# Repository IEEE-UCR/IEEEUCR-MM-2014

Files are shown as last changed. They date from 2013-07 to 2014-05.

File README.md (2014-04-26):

IEEEUCR-MM-2014
===============

In order to create better, exciting micromice, it is necessary to pool together work in order to create better programs to run on micromice.

This repository has folders for all current micromice.  Some may have been abandoned in favor of better mice (refmouse V1).

Although it is difficult to admit to the utter data-copying, a lot of the kicad libraries are copied.

Within the hardware realm, KiCAD is the de facto standard for making PCBs.  When micromice get really big, it's absolutely essential to choose a program that allows multipage schematics.

And through these methods, we will create better micromice.

Documentation is also provided through the documentation folder... in case anybody wants to read it.

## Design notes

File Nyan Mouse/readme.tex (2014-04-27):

\documentclass{article}
\usepackage[UKenglish]{babel}
\usepackage{parskip}
\usepackage{indentfirst}
\setlength{\parindent}{15pt}
\usepackage{fullpage}
\setcounter{tocdepth}{3}
\begin{document}
\title{Nyan Mouse Readme}
\author {Brandon Lu} \date{\today}
\maketitle
\begin{abstract}
Nyan Mouse is made to display Nyan Cat like blinking and audio.  From a hardware perspective, Nyan Mouse will offer an FPGA with a Nios II processor implemented on it along with some peripherals for quaterature decoding (including count and inter-step delay for speed).  Everything should be capable of parallel-execution including maze solving.  Maze solving, due to time constraints, will not be implemented in a hardware accelerated form.  This will be Brandon's micromouse entry for 2014 if it is completed.  Otherwise, Overvolt will be the micromouse of choice for racing.
\end{abstract}

\section {Introduction}
Micromouse as a competition creates an environment that requries the harmonious marriage between hardware and software.  There are many arguments that feature software or hardware as the superior micromouse success determiner, but in the end a micromouse simulator that is beautifully coded exists only in the computer and a hardware implementation with the best hardware imaginable including support for wall decoding and time delayed illumination is only a brainless device that goes forward nonstop at an unimaginable speed (probably to crash into the wall ahead of it).  Micromouse is not a simple thing to do in any sense unless one decides to make it simple (and ignore the fine detail present in any of the advanced topics which it can cover).  The most important thing to have during micromouse is probably time management; humans -- especially college humans -- are only given a finite amount of time on micromouse.  It is possible to extract time from other things, but that can end in disaster quite easily.

\section {Implementing the Cat}
\subsection {Hardware}
The hardware on this micromouse is fairly complex and a full explanation of the hardware cannot be achieved easily.

In short, the main board contains the non-controller parts of nyan mouse.  This includes parts such as the motors, drive train, encoders, speakers, LEDs, and other rather important parts that have absolutely nothing to do with making a functional micromouse but instead add quirky features to a micromouse.

\subsection {Software}
The software on this mouse will be my old software that ran on Overvolt.
The software is actually quite craptastinc in that it does not support full encoder guidance or mapping.
In fact, only one encoder was used because of circuit design errors encountered while not considering the therevin equivalence models of the quaterature encoders inside the Faulhaber motors.

\section {Nyaning and Catting (Methods)}
Nyanning and catting is achieved with the use of CAD software and implementation of the \textit{Cyclone IV Handbook} along with various application notes such as those from Spansion (which creates the flash ROM).

Autodesk Inventor 2013 is used to do the 3D design of the micromouse (and will hopefully do the printed circuit board stacks as well).

Altera Quartus is used to instantiate the FPGA internals including the Nios II cores.

Altera Nios II developer (based on eclipse) is used to program the Nios II processor and generate the programming files.

KiCAD is used to generate the actual printed circuit boards (this makes a significant portion of available PDF documentation because of the ease in exporting KiCAD to schematic).

\section {Is there any win to this game?}
Nyan Cat as a game itself (if one can consider it a game), has no end but a definite beginning.  By default, the counter on the nyan cat webpage will keep incrementing (perhaps until it overflows at some very large number).  The purpose of this document was to explain what one would find in the micromouse folder and how it's supposed to work, but I forgot to do that and instead went on about the philosophy of micromouse.

\end {document}

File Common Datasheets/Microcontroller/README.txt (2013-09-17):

Our microcontroller will most likely be the STM32F4
http://www.st.com/web/en/catalog/mmc/FM141/SC1169/SS1577

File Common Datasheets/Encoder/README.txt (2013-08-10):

IEEE UCR has decided to, on its first mouse at least, use a precision magnet and a 10bit magnetic rotary decoder.

Magnetic Rotary Position Sensor: http://www.ams.com/eng/Products/Magnetic-Position-Sensors/Rotary-Magnetic-Position-Sensors/AS5040

Precision Magnet: http://www.ams.com/eng/Products/Magnetic-Position-Sensors/Magnets3/AS5000-MD6H-3

Somebody who has already done this before: http://xmog123x.blogspot.com/2012/11/kirin-micromouse.html

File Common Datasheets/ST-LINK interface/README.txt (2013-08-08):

How we do STLink
================

The STLink adapter interfaces to a boxed 2x10 header with 2.54mm (1 mil) pitch.  This interface is too large for our purposes.

So instead we have a 1.0mm device interfacing to these signals.

When the time comes, we will have a device interface on the IEEUCR website for all to use.

"At this point 8/8/2013 I have no idea how to use STLink" -- Brandon.

It should be noted that although we do have a SWIM interface that we could use instead of the 20 pin awesomeness, we need debugging.

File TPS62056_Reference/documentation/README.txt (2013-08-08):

Voltage Regulator
=================

The voltage regulation circuit is designed to be portable across different KiCAD builds of micromouse.

This folder contains our reference board and some PDF's.  We may have some waveforms available for it too.

Our test results show a clearly bruteforceable and well designed regulator.

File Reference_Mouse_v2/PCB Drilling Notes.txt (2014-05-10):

Bluetooth header has traces going to the top

Drill bit sizes
Pin headers: 1.00mm
LED/PTH leads: 0.70mm
Via holes: 0.6mm

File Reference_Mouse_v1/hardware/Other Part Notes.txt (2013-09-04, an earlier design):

[LED Alphanumeric Display]
Avago HCMS-39xx series (HCMS-29xx series is the 5v-powered version)
5x7 dot matrix
Basically a giant shift register for each pixel + some control registers 
Easily drivable using SPI + DMA
Example: http://www.micromouseonline.com/2012/03/11/adding-dma-to-the-spi-driver-with-the-stm32f4/#axzz2cIIhLh9E

[Motor Drivers]
DRV8837
Control inputs (each)
	IN1 & IN2 (internal pulldowns)

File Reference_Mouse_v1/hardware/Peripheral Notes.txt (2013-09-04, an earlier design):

[Timer assignments]
TIM1 (Advanced control)
	Motor PWM x 2

TIMx (general purpose)
	Quadrature decoder x 1

TIMx (general purpose)
	Quadrature decoder x 1

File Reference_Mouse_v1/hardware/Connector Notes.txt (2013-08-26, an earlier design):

It seems like every small DC connector attached to a battery gets called a "JST", which is not very helpful.
http://www.rcgroups.com/forums/showthread.php?t=1493712

Lipo balance plugs are always "JST-XH"
	Easily recognized: 2.5mm pitch and "hooks" on the plug and recepticicle
	PCB-mount top-entry receptacle is B3B-XH-A (not B3B-XH-AM, that one has board-insertion orientation pin)
	Bal-plug pinout: http://goo.gl/ZAvH9i
		I'm going to call the top pin #1 so it stays GND

The protected 1S lipos and accessories sold by Sparkfun are NOT JST-XH (they are some other 2mm pitch JST)
	(Their 2S RC-style packs, however, do have JST-XH balance connectors)

The 2-pin red "JST" with beveled edges on the top?
	Those are actually "RCY connectors", manufactured by JST
	These are wire-to-wire only. There does not seem to be a PCB-mount version of these

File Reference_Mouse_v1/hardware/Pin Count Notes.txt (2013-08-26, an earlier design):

[Estimated Pin Count Requirement]

* 6 IR sensor pairs
1-6 (6):  IR Emitters enable
7-12 (6): IR Detectors ADC

* 2 motors with quadrature encoders"
* 3 pins per motor allows flexible drive topologies (sign-mag, locked antiphase, etc)
13-16 (2x2): Wheel Encoders, quadrature
17-22 (2x3): Motor drivers

* SPI devices
23-25 (3): SPI bus (MOSI, MISO, SCK)
26-27 (2): Avago serial display (Chip select, Register select)

* I2C devices
28-29 (2): I2C bus (SCK, SDA)
	MPU-6050 Gyro + Accel (400 KHz, 2.38V-3.46V)
	HMC5883L Mag (400 KHz, 2.16V-3.6V)
	Run I2C bus and devices off 2.8V linreg? STM32 capable of 2.8V levels.

30-31 (2): UART (TX, RX)
	Bluetooth + serial bootload ("JY-MCU")

32 (1): MPU-6050 Interrupt

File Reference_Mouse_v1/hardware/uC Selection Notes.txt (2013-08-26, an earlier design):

[STM32 F1 Line - Cortex M3]
STM32F100 Value line  – 24 MHz CPU with motor control and CEC functions
STM32F101 – 36 MHz CPU, up to 1 Mbyte of Flash
STM32F102 – 48 MHz CPU with USB FS
STM32F103 – 72 MHz, up to 1 Mbyte of Flash with motor control, USB and CAN
STM32F105/107 – 72 MHz CPU with Ethernet MAC, CAN and USB 2.0 OTG

STM32VLDISCOVERY chip is STM32F100RB
Maple chip is STM32F103RB (LQFP64)
	"Medium density"
	* 72 MHz Cortex-M3
	* 128 KB flash
	* 20 KB SRAM
	* 3 GP timers
	* 1 Adv. control timers
	* 2 x SPI
	* 2 x I2C
	* 3 x USART
	* USB
	* CAN bus
	* 51 GPIOs
	* 2 x 12-bit adc, 16 channels
	* 2.0V to 3.6V

[STM32 F4 Line - Cortex M4F]
STM32F4DISCOVERY chip is STM32F407VGT6 (LQFP100)

Alternatively, use STM32F405RG (LQFP64)
	Same core and peripherals
	Smaller package, to match F1 drop-in replacement
	Still more than enough ADC channels and GPIOs
	No external memory controller, but not needed
	* 168 MHz Cortex-M4F
	* 1 MB flash
	* 192 KB SRAM
	* 10 GP timers
	* 2 Adv. control timers
	* 2 Basic timers
	* Random number gen
	* 3/2 (f/d) x SPI
	* 3 x I2C
	* 4/2 x USART
	* USB
	* 51 GPIOs
	* 3 x 12-bit adc, 16 channels
	* 1.8V to 3.6V

http://www.micromouseonline.com/2009/12/29/arm-stm32-jtag/#axzz2cJiC3gTI

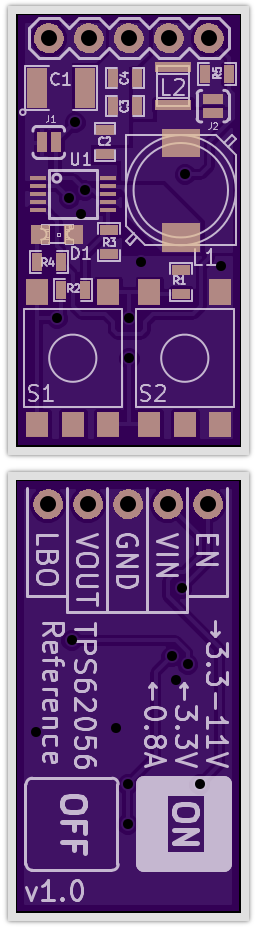
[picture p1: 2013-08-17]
TPS62056_Reference/hardware/Oshpark Preview.PNG

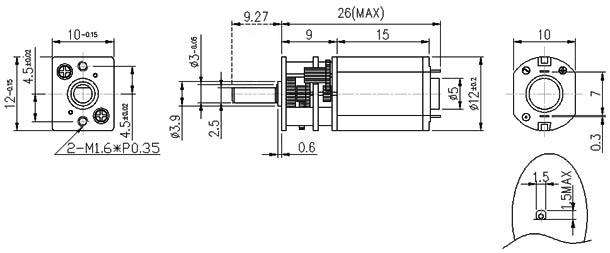
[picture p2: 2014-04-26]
Common Datasheets/Motor/Pololu Micro Metal Gearmotor Dimensions (similar to Sanyo).png

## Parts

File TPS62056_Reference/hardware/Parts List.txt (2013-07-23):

----[ Notes ]----

Ripple at 8.4v to 3.3v w/ 10uH inductor
0.24A

Module pinout:
1. Enable                 _
2. Vin (3-pin regulator)   |
3. Gnd (3-pin regulator)   | Silkscreen box
4. Vout (3-pin regulator) _|
5. Low-Battery Out

----[ User Manual ]----

Things to add to your circuit:

Reverse polarity protection:
In the form of a low-voltage drop diode or MOSFET-based circuit
Why is it not in the module?
Both of the above mentioned components introduce some form of inefficiency and cost more.
Diodes have a voltage drop, MOSFETs have on-resistance and 
In addition, you will most likely connect your motor drivers directly to the battery
while the switching regulator powers the logic and sensors. Integrating reverse polarity protection into the module will not protect those components.
If you want, you can add a diode to your circuit while you prototype or final circuit
But you should use polarity-coded connectors for your batteries anyway.
And just be careful.

Saving power:
The power LED lets you see at a glace whether the circuit is powered. But if your project needs to run for the longest time posible on a battery charge, this will save a few mA.

Not populating the LBI voltage divider nor the LBO pull-up will net you few microamps, but this should rarely be necessary.

Staying on:
If you already have an external power switch, shorting J1 and not popluating either pushbutton will cause the module to turn on whenever power is applied, thus acting like a regular 3-pin regulator.

Software-controlled shutdown:
Using an additional transistor, you can have your microcontroller turn off it's own power by momentarily pulling the Enable pin to ground through a 10K resistor. The resistor prevents a battery-to-ground short if the module's "On" button is pressed at the same time). The pushbutton causes full battery voltage to appear on the Enable pin, do not connect the enable pin directly to your microcontroller.
[insert diagram here]

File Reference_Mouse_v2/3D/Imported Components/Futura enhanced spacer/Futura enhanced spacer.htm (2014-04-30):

Autodesk Inventor Translation Report | Monday, April 28, 2014 (6:05 PM)
Source File: | C:\Users\Kevin\Downloads\futura-3D-printing-model\Futura enhanced spacer.stl
Translator Type: | STL | Sending System:
Author: |  | Translation Time: | 00:00:02
Options
Import Type: | N/A
Entity Types to Import: | Meshes
Import into Repair Environment: | N/A
Import Assembly as Single Part: | N/A
Create Surfaces As: | N/A
Import Multiple Solid Parts as Assembly: | N/A
Check Parts during Load: | N/A
Auto Stitch: | N/A
Enable Advanced Healing: | N/A
Color Red/Green/Blue Order: | RGB
+/- | Name | Inventor File | Status
[ ] | Futura enhanced spacer.ipt | C:\Users\Kevin\Dropbox\IEEEUCR-MM-2014\Reference_Mouse_v2\3D\Imported Components\Futura enhanced spacer\Futura enhanced spacer.ipt | Successful

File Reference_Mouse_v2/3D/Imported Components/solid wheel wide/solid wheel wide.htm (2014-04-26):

Autodesk Inventor Translation Report | Wednesday, April 23, 2014 (12:45 AM)
Source File: | C:\Users\Kevin\Downloads\futura-3D-printing-model\solid wheel wide.stl
Translator Type: | STL | Sending System:
Author: |  | Translation Time: | 00:00:00
Options
Import Type: | N/A
Entity Types to Import: | Meshes
Import into Repair Environment: | N/A
Import Assembly as Single Part: | N/A
Create Surfaces As: | N/A
Import Multiple Solid Parts as Assembly: | N/A
Check Parts during Load: | N/A
Auto Stitch: | N/A
Enable Advanced Healing: | N/A
Color Red/Green/Blue Order: | RGB
+/- | Name | Inventor File | Status
[ ] | solid wheel wide.ipt | C:\Users\Kevin\Dropbox\IEEEUCR-MM-2014\Reference_Mouse_v2\3D\Imported Components\solid wheel wide\solid wheel wide.ipt | Successful

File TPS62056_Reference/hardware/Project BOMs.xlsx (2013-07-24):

Supplier | Supplier Part # | Description | Package | Designators | Cost / Unit | Qty / Board | Item Cost / Board | Total Qty | Notes
Mouser | 810-C3225Y5V1C226Z-9 | MLCC 22uF, 16V, 20% | 1210 | C1 | $0.29 | 1 | $0.29 | 3
Mouser | 810-C1608X5R0J226M | MLCC 22uF, 6.3V, 20% | 0603 | C2, C3, C4 | $0.15 | 3 | $0.45 | 9
Mouser | 720-LSR976-NR-1 | LED Red Clear Diffused Std., 2.0V, 25mA | 0805 | D1 | $0.05 | 1 | $0.05 | 3 | (Quantity 10 price bracket)
Mouser | 652-SRR7032-100M | Inductor 10uH Shielded, 20%, 1.4A, 0.068ohm | (non-std.) | L1 | $0.64 | 1 | $0.64 | 3 | http://www.mouser.com/ds/2/54/SRR7032-54455.pdf
Mouser | 542-PM1008-82NK-RC | Inductor 82nH Unshielded, 10%, 1A, 0.22ohm | (non-std.) | L2 | $0.29 | 1 | $0.29 | 3
Mouser | 517-5111TG | Pin Header 40-pin, right-angle 0.1", gold | SIL-5 | P1 | $1.66 | 0.125 | $0.21 | 0.375 | Broken off of a 40-pin header. Can also use straight headers or no headers at all.
Mouser | 667-ERJ-3GEYJ475V | Resistor 4.7 MΩ, 5% | 0603 | R1 | $0.01 | 1 | $0.01 | 3 | (Quantity 10 price bracket)
Mouser | 667-ERJ-3GEYJ514V | Resistor 510 KΩ, 5% | 0603 | R2, R5 | $0.01 | 2 | $0.02 | 6 | (Quantity 10 price bracket)
Mouser | 667-ERJ-3GEYJ114V | Resistor 110 KΩ, 5% | 0603 | R3 | $0.01 | 1 | $0.01 | 3 | (Quantity 10 price bracket)
Mouser | 667-ERJ-3GEYJ331V | Resistor 330 Ω, 5% | 0603 | R4 | $0.01 | 1 | $0.01 | 3 | (Quantity 10 price bracket)
Mouser | 688-SKHMQKE010 | Tactile Switch SMD, NO, 0.98N, Black | (non-std.) | S1, S2 | $0.24 | 2 | $0.48 | 6
Mouser | 595-TPS62056DGS | TPS62056 3.3V Switching Regulator | miniSO-10 | U1 | $3.05 | 1 | $3.05 | 3
Oshpark | (n/a) | PCB | (n/a) | (n/a) | $3.05 | 0.3333 | $1.02 | 0.9999 | Comes as a set of three
 |  |  |  |  |  |  | $0.00 | 0
 |  |  |  |  |  |  | $0.00 | 0
 |  | (All items are priced at quantity 1 unless |  |  |  |  | $0.00 | 0
 |  | otherwise noted) |  |  |  |  | $0.00 | 0
 |  |  |  |  |  |  | $0.00 | 0
 |  |  |  |  |  |  | $0.00 | 0
 |  |  |  |  |  |  | $0.00 | 0
 |  |  |  |  |  |  | $0.00 | 0
 |  |  |  |  |  |  | $0.00 | 0
 |  |  |  |  |  |  | $0.00 | 0
 |  |  |  |  |  |  | $0.00 | 0
 |  |  |  |  |  |  | $0.00 | 0
 |  |  |  |  |  |  | $0.00 | 0
 |  |  |  |  |  |  | $0.00 | 0
 |  |  |  |  |  |  | $0.00 | 0
 |  |  |  |  |  |  | $0.00 | 0
 |  |  |  |  |  |  | $0.00 | 0
 |  |  |  |  |  |  | $0.00 | 0
 |  |  |  |  |  |  | $0.00 | 0
 |  |  |  |  |  |  | $0.00 | 0
 |  |  |  |  |  |  | $0.00 | 0
 |  |  |  |  |  |  | $0.00 | 0
 |  |  |  |  |  |  | $0.00 | 0
 |  |  |  |  |  |  | $0.00 | 0
 |  |  |  |  |  |  | $0.00 | 0
 |  |  |  |  |  |  | $0.00 | 0
 |  |  |  |  |  |  | $0.00 | 0
 |  |  |  |  |  |  | $0.00 | 0
Cost / Item: The cost of one component of this type. (the cost of a single resistor) |  |  |  | Subtotal per board: |  |  | $6.52
Qty / Board: The count of this component that is present on a single board |  |  |  | (n*) Number of boards: |  |  | 3
Item Cost / Board: The combined cost of every one of this component on a single board |  |  |  | Total: |  |  | $19.55
Total Qty: The number of this component that should be ordered to populate n* boards
(Highlight colors chosen by colorblind person. Your milage may vary.)

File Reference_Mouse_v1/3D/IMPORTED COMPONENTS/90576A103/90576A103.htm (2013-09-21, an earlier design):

Autodesk Inventor Translation Report | Saturday, September 21, 2013 (2:42 AM)
Source File: | E:\ENGINEERING\IEEEUCR-MM-2014\HARDWARE\REFERENCE_MOUSE_V1\3D\SOLIDWORKS MCMASTERCARR PARTS\90576A103.SLDPRT
Translator Type: | SolidWorks | Sending System: | SolidWorks 2007
Author: |  | Translation Time: | 00:00:01
Options
Import Type: | N/A
Entity Types to Import: | Solids, Surfaces, Wires
Import into Repair Environment: | Yes
Import Assembly as Single Part: | No
Create Surfaces As: | Single Composite Feature
Check Parts during Load: | No
Auto Stitch: | No
Enable Advanced Healing: | N/A
+/- | Name | Inventor File | Status
[ ] | 90576A103 | E:\ENGINEERING\IEEEUCR-MM-2014\HARDWARE\REFERENCE_MOUSE_V1\3D\SOLIDWORKS MCMASTERCARR PARTS\IMPORTED COMPONENTS\90576A103\90576A103.IPT | Successful

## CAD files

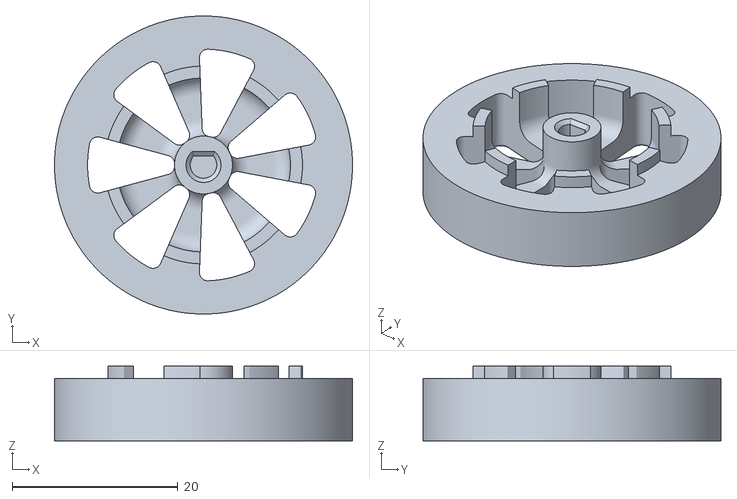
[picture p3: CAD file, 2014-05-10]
Reference_Mouse_v2/3D/Wheel Printable.stl
36.0 x 36.0 x 9.00

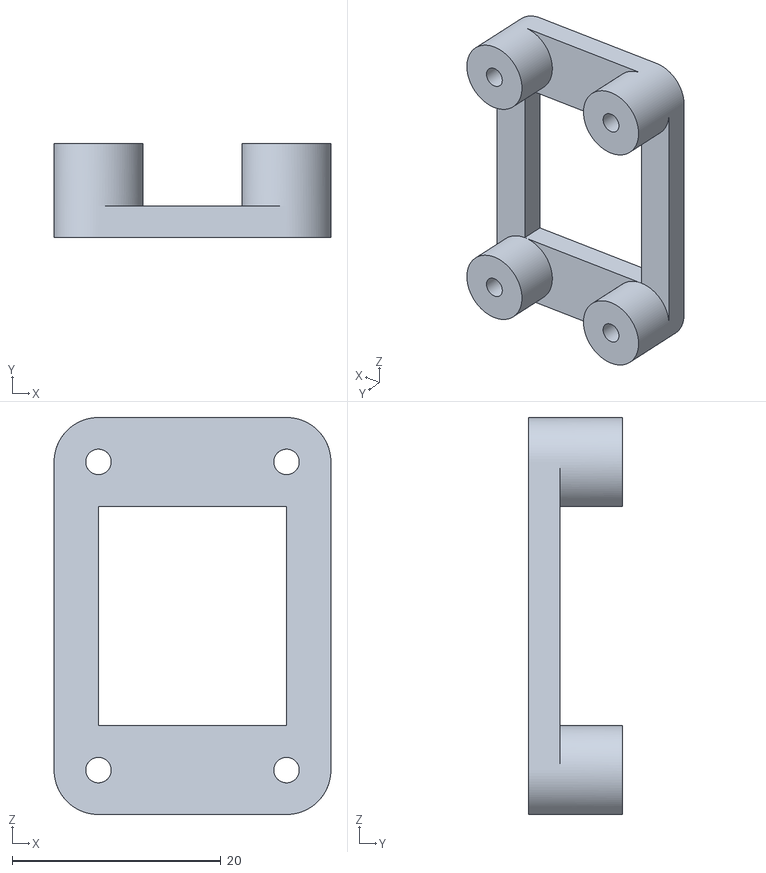
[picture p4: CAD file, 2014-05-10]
Reference_Mouse_v2/3D/Spacer.stl
26.5 x 9.00 x 38.0

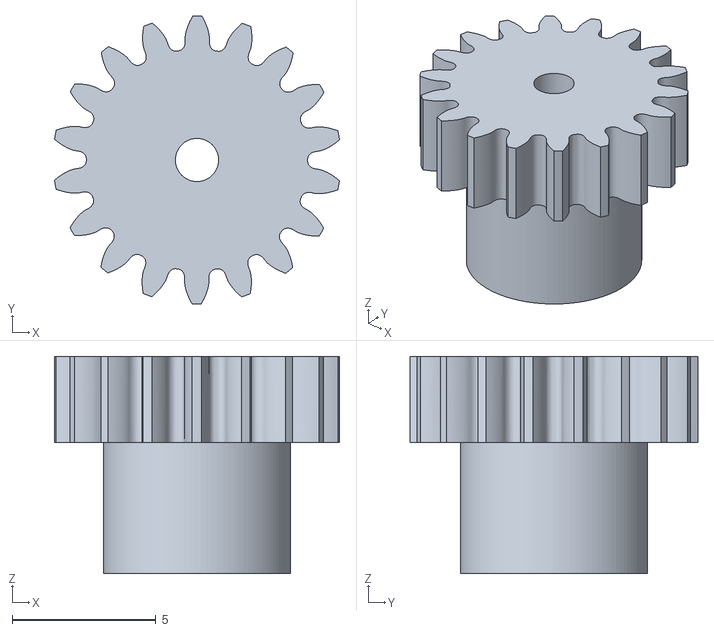
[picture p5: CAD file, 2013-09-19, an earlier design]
Reference_Mouse_v1/3D/mount_gear motor_5.stl
9.90 x 10.00 x 7.55

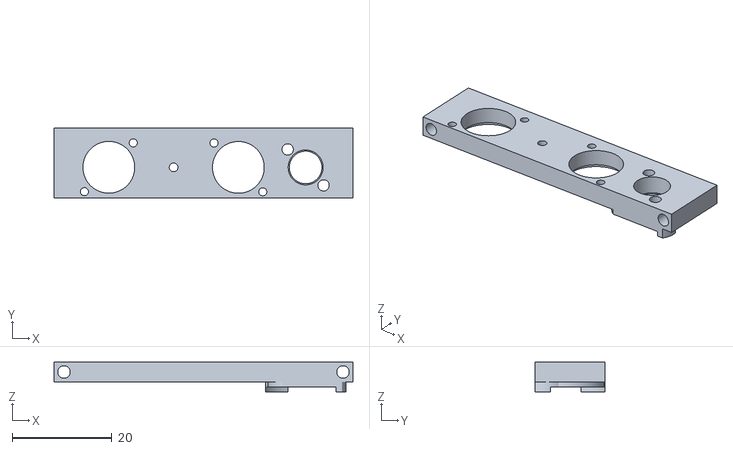
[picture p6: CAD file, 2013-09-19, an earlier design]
Reference_Mouse_v1/3D/mount_mount_4.stl
60.0 x 14.0 x 6.00

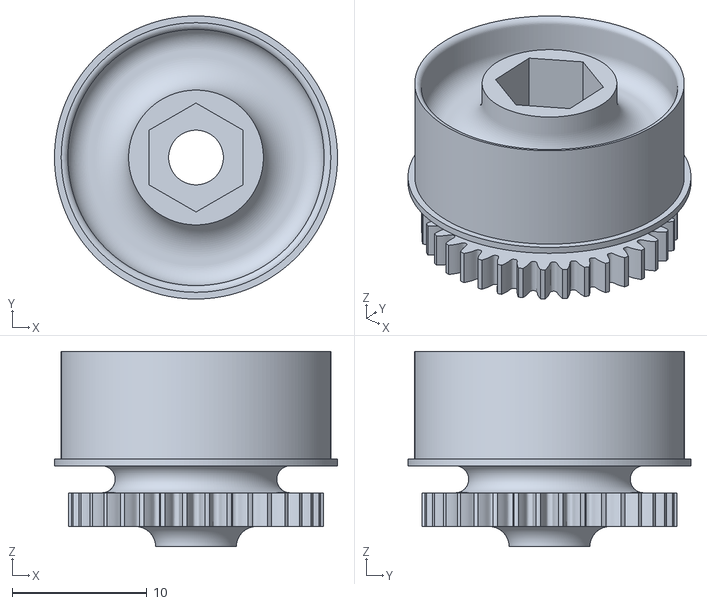
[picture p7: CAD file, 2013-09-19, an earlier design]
Reference_Mouse_v1/3D/mount_Wheel_MIR_3.stl
21.0 x 21.0 x 14.5

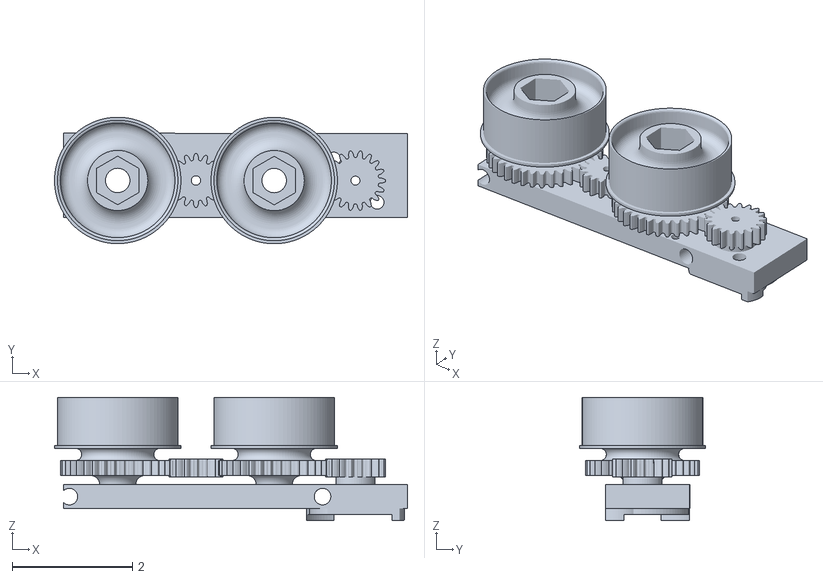
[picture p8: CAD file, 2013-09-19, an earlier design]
Reference_Mouse_v1/3D/mount.stl
5.86 x 2.10 x 2.05

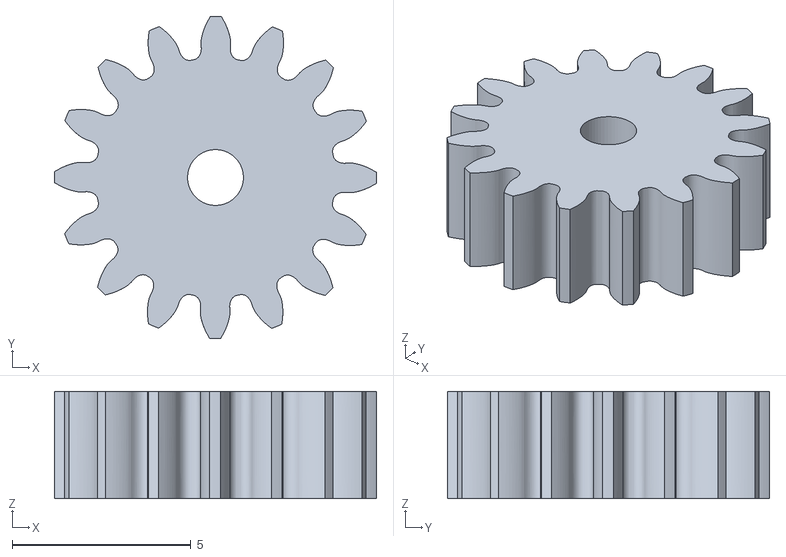
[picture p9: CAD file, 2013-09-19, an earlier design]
Reference_Mouse_v1/3D/mount_Wheel2Wheel_2.stl
9.00 x 9.00 x 3.00

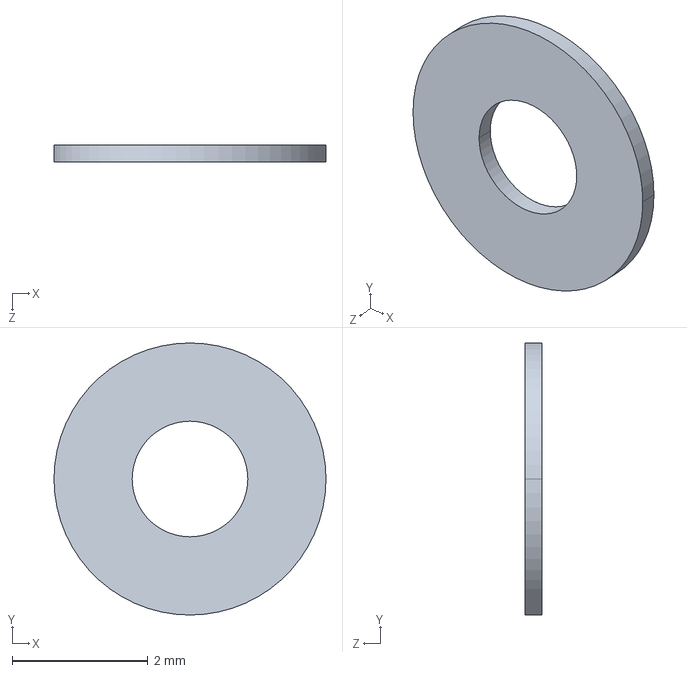
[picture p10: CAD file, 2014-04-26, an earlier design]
Reference_Mouse_v1/3D/McMasterCarr Parts/91166A170.STEP
4.00 x 4.00 x 0.25 mm

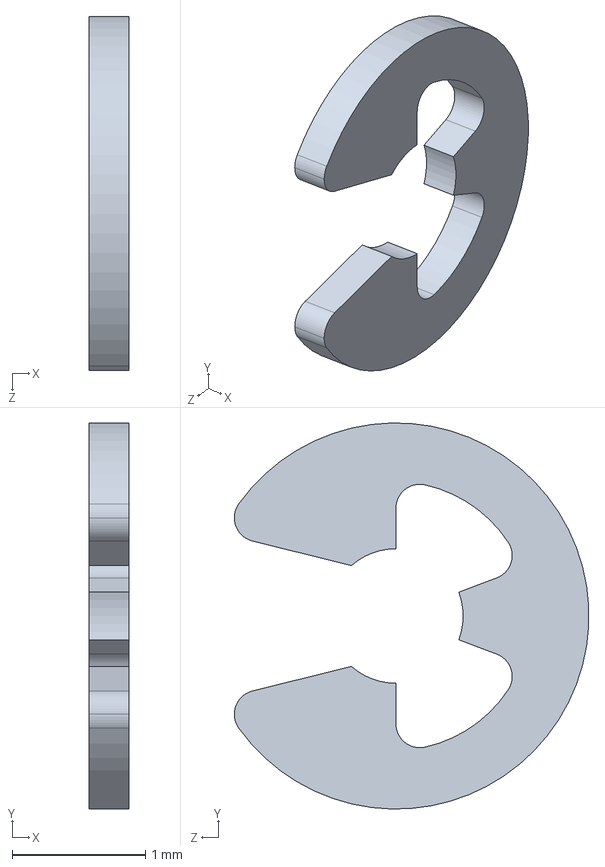
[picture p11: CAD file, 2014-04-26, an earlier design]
Reference_Mouse_v1/3D/McMasterCarr Parts/98543A060.STEP
0.3 x 2.90 x 2.66 mm

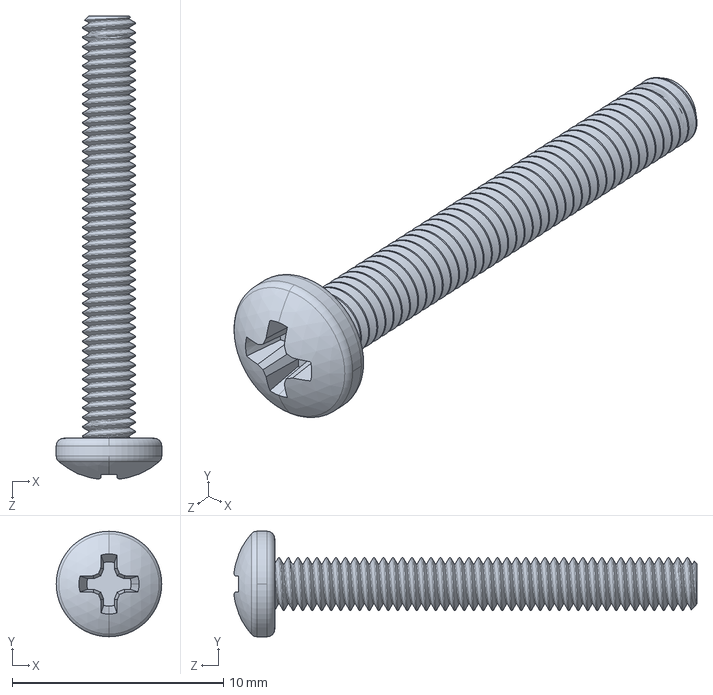
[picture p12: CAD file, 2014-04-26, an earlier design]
Reference_Mouse_v1/3D/McMasterCarr Parts/92005A077.STEP
5.00 x 5.00 x 21.9 mm

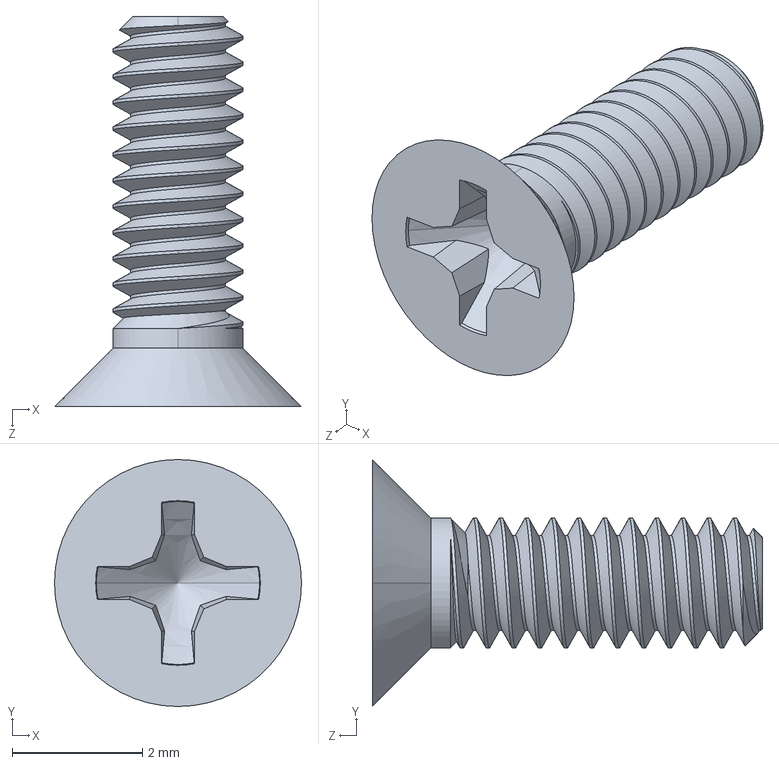
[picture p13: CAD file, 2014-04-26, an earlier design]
Reference_Mouse_v1/3D/McMasterCarr Parts/92010A003.STEP
3.80 x 3.80 x 6.00 mm

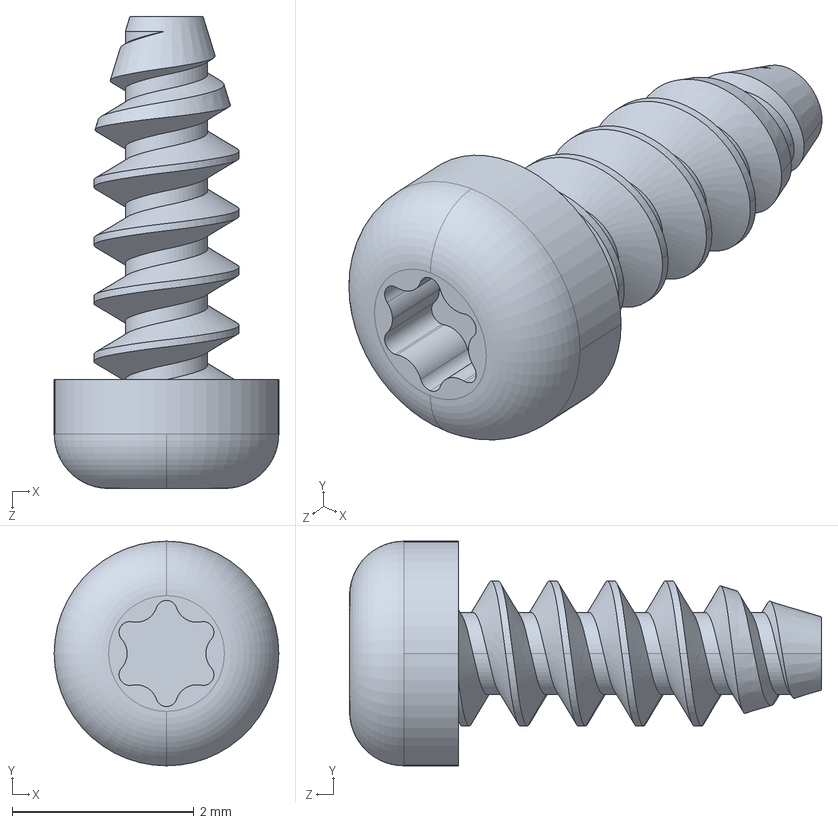
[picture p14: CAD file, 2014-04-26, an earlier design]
Reference_Mouse_v1/3D/McMasterCarr Parts/96817A113.STEP
2.48 x 2.48 x 5.20 mm

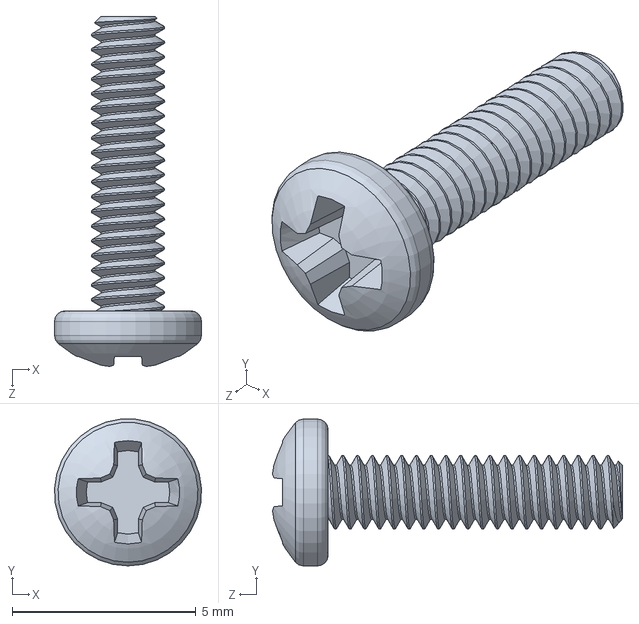
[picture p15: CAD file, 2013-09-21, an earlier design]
Reference_Mouse_v1/3D/McMasterCarr Parts/92005A029.SLDPRT
3.99 x 3.99 x 9.51 mm

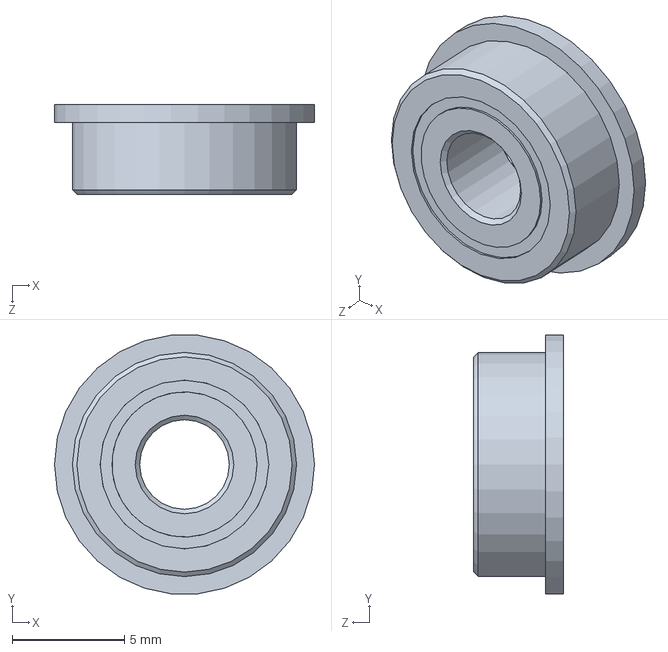
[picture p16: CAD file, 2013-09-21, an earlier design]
Reference_Mouse_v1/3D/McMasterCarr Parts/7804K129.SLDPRT
11.6 x 11.5 x 4.00 mm

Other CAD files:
Reference_Mouse_v1/3D/mount_Wheel_1.stl
Reference_Mouse_v1/3D/McMasterCarr Parts/92095A197.SLDPRT
Reference_Mouse_v1/3D/McMasterCarr Parts/90576A103.SLDPRT
Reference_Mouse_v1/3D/McMasterCarr Parts/92005A076.SLDPRT
Reference_Mouse_v1/3D/IMPORTED COMPONENTS/7804K129/7804K129.IPT
Reference_Mouse_v1/3D/IMPORTED COMPONENTS/7804K129/OldVersions/7804K129.0002.IPT
Reference_Mouse_v1/3D/IMPORTED COMPONENTS/90576A103/90576A103.IPT
Reference_Mouse_v1/3D/IMPORTED COMPONENTS/90710A025/90710A025.IPT
Reference_Mouse_v1/3D/IMPORTED COMPONENTS/92005A029/92005A029.IPT
Reference_Mouse_v1/3D/IMPORTED COMPONENTS/92005A076/92005A076.IPT
Reference_Mouse_v1/3D/IMPORTED COMPONENTS/92005A077.IPT
Reference_Mouse_v1/3D/IMPORTED COMPONENTS/92095A197/92095A197.IPT
Reference_Mouse_v1/3D/IMPORTED COMPONENTS/92095A197/OldVersions/92095A197.0001.IPT
Reference_Mouse_v1/3D/Kingbright_WP7113F3BT_Emitter.ipt
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

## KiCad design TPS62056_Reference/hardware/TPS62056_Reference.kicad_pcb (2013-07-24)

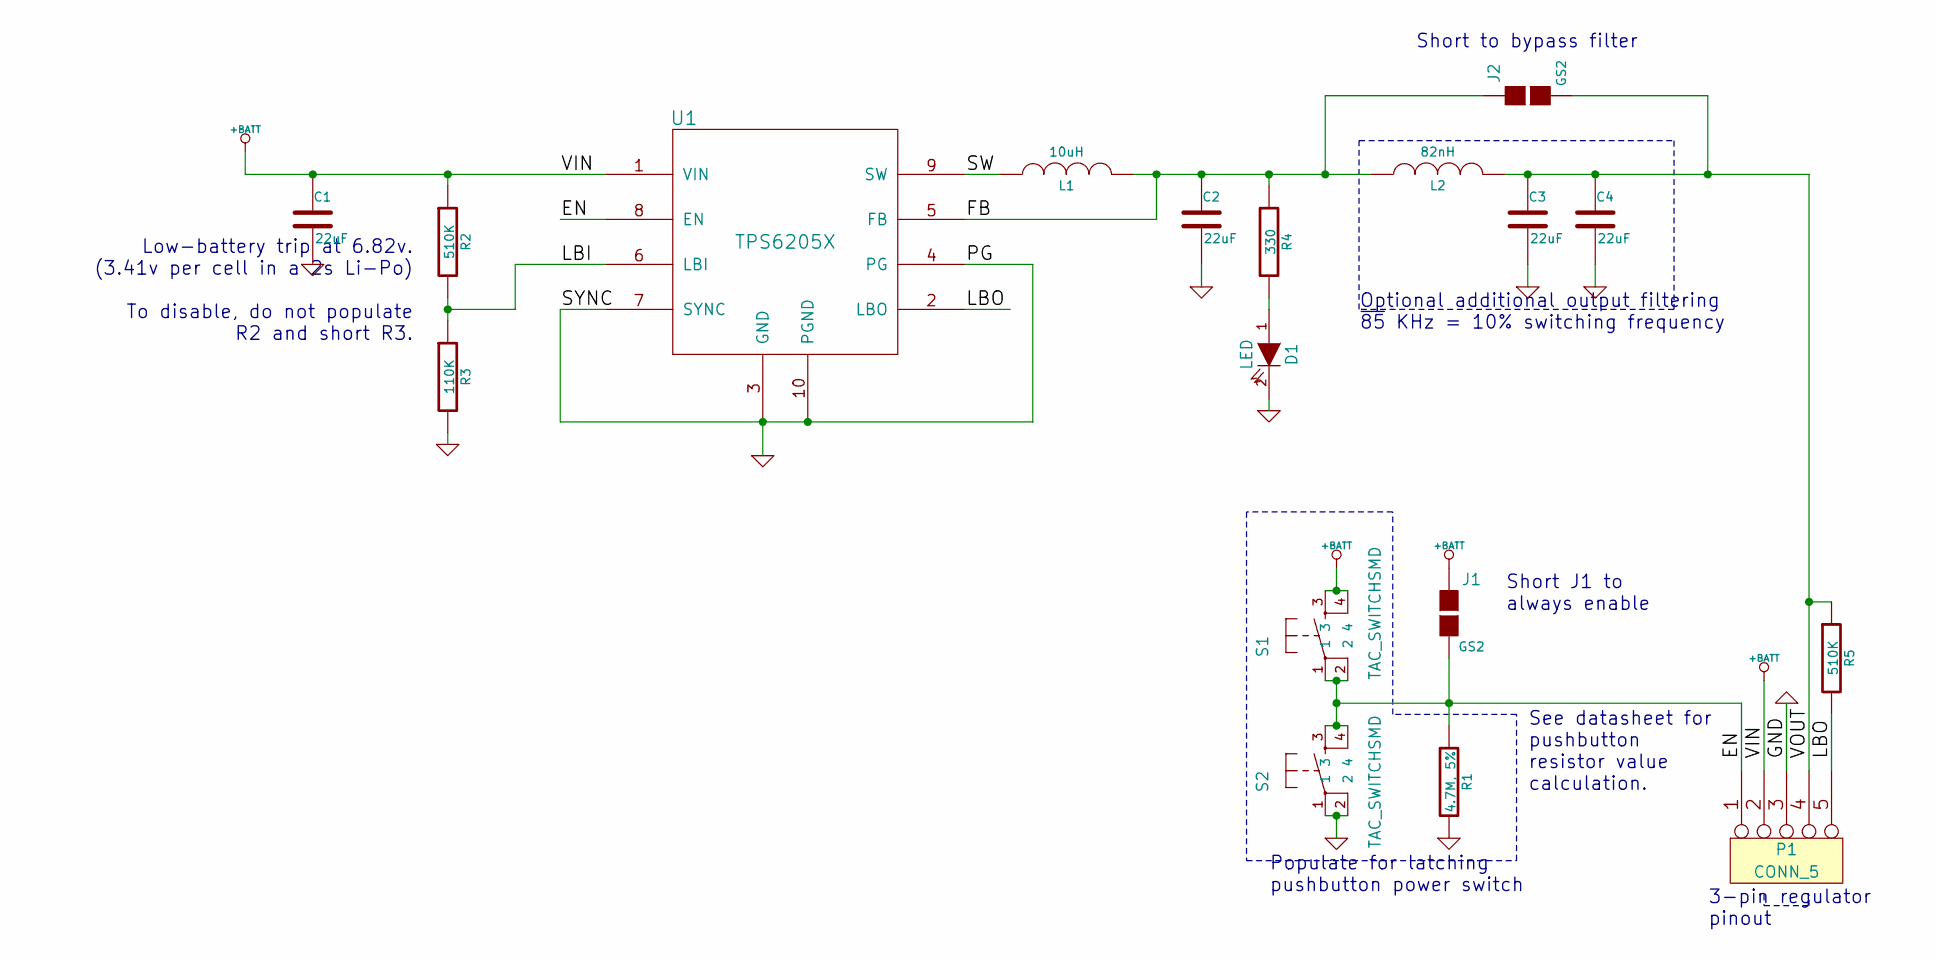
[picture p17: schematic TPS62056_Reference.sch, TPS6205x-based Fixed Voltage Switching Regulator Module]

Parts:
C1, C2, C3, C4: 22uF
D1: LED
J1, J2: GS2
L1: 10uH
L2: 82nH
P1: CONN_5
R1: 4.7M, 5%
R2, R5: 510K
R3: 110K
R4: 330
S1, S2: TAC_SWITCHSMD; SparkFun-TACTILE_SWITCH_SMD
U1: TPS6205X

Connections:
+BATT: C1.1, J1.1 (G1), P1.2, R2.1, S1.3, S1.4, U1.1 (VIN)
/EN: J1.2 (G2), P1.1, R1.1, S1.1, S1.2, S2.3, S2.4, U1.8 (EN)
/FB: C2.1, J2.1 (G1), L1.2, L2.1, R4.1, U1.5 (FB)
/LBI: R2.2, R3.1, U1.6 (LBI)
/LBO: P1.5, R5.2, U1.2 (LBO)
/SW: L1.1, U1.9 (SW)
/VOUT: C3.1, C4.1, J2.2 (G2), L2.2, P1.4, R5.1
GND: C1.2, C2.2, C3.2, C4.2, D1.2 (K), P1.3, R1.2, R3.2, S2.1, S2.2, U1.3 (GND), U1.4 (PG), U1.7 (SYNC), U1.10 (PGND)
unnamed: D1.1 (A), R4.2

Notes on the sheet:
Short J1 to always enable
Populate for latching pushbutton power switch
Low-battery trip at 6.82v. (3.41v per cell in a 2s Li-Po) To disable, do not populate R2 and short R3.
3-pin regulator pinout
See datasheet for pushbutton resistor value calculation.
Optional additional output filtering ~85 KHz = 10% switching frequency
Short to bypass filter

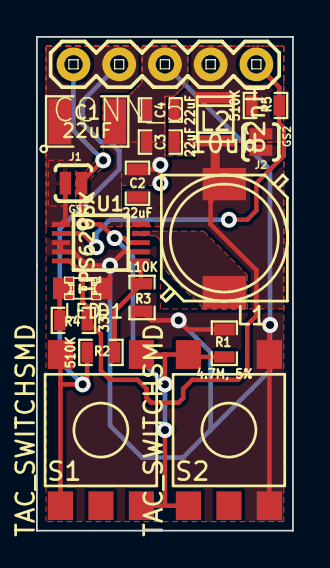
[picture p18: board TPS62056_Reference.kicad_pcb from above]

Board: 2 copper layers, 14.2 x 27.4 mm, 18 parts (0 on the bottom side), 9 nets.

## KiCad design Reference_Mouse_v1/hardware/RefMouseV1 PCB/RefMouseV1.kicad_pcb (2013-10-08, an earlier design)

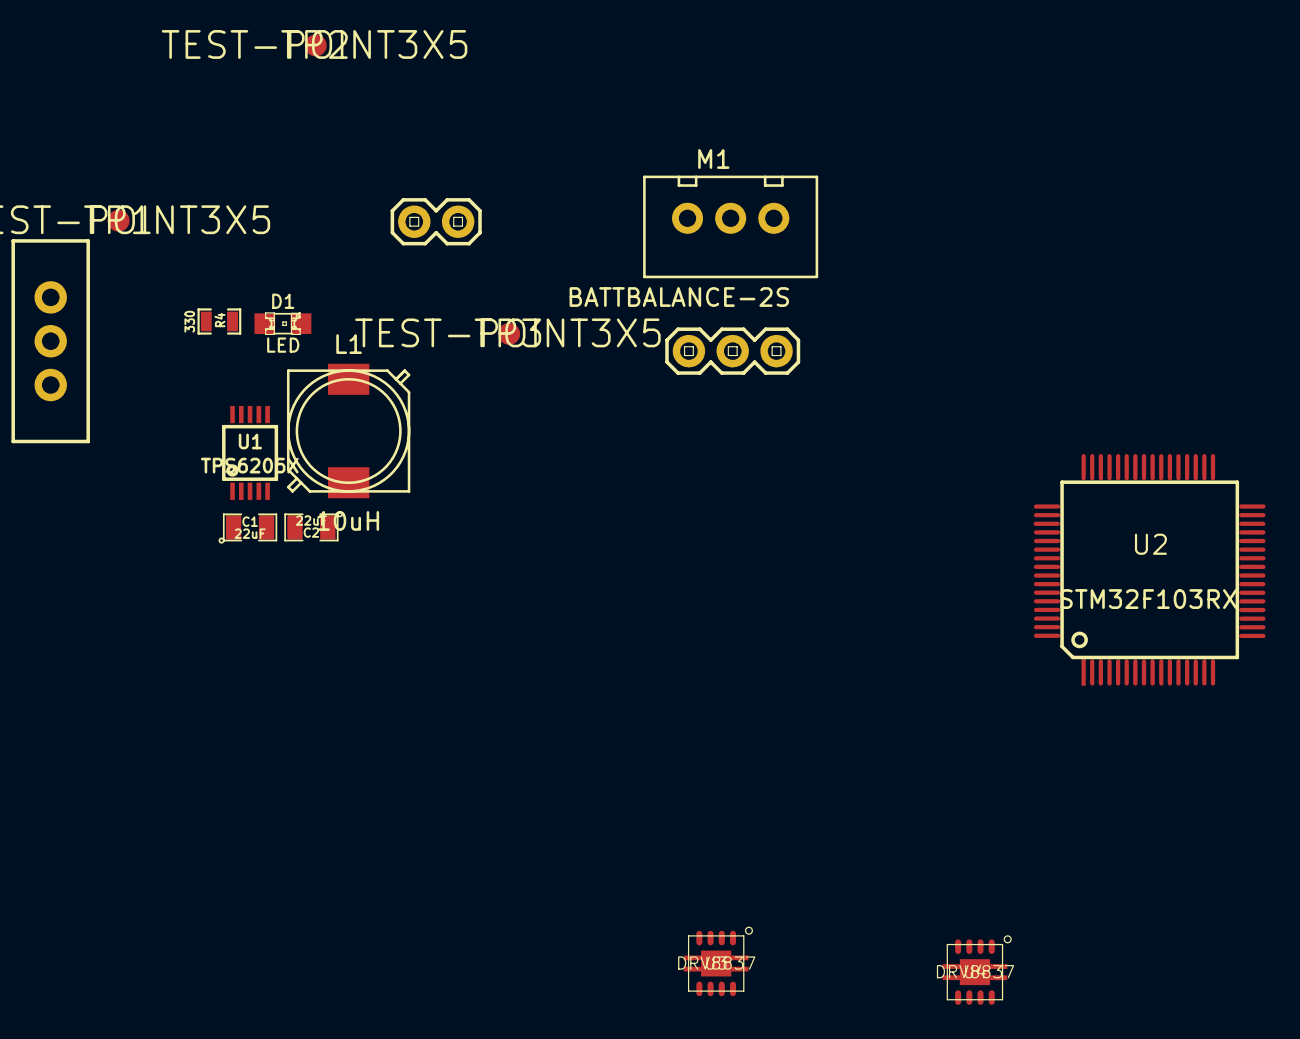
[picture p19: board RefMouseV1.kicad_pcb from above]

Board: 2 copper layers, 16 parts (0 on the bottom side), 9 nets, no tracks yet.

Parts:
C1, C2: 22uF; SM0805
D1: LED; LED-0805
JP1: M03PTH; SparkFun-1X03
JP2: M02PTH; SparkFun-1X02
L1: 10uH; Bourns_SRR7032
M1: BATTBALANCE-2S; B3B-XH-A
R4: 330; SM0603_Resistor
S1: SWITCH-SPSTPTH; SparkFun-SWITCH-SPDT
TP1, TP2, TP3: TEST-POINT3X5; SparkFun-PAD.03X.05
U1: TPS6205X; MSOP10-0.5
U2: STM32F103RX; TQFP_64
U3, U4: DRV8837; S-PWSON-N8

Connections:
/Motor/V_LOGIC: U3.7, U3.8, U4.7, U4.8
/Motor/V_MOTOR: U3.1, U4.1
/Power/+3.3V: C2.1, L1.2, R4.1, U1.5
/Power/SW: L1.1, U1.9
/Power/VBATT: C1.1, JP1.3, M1.3, S1.1, U1.1
/Power/VBATT_SW: S1.2, U1.8
GND: C1.2, C2.2, D1.2, JP1.1, JP2.1, JP2.2, M1.1, S1.3, U1.3, U1.4, U1.6, U1.7, U1.10, U2.63, U3.4, U4.4
unnamed: D1.1, R4.2
unnamed: JP1.2, M1.2

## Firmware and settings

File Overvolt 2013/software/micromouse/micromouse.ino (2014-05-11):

/* TODO
 *
 ** Implement new sensor scheme
 * Sensors
 *  \/
 * Position control
 *  \/
 * Veocity control
 *
 ** Implement pulse sensor measurements
 ** Implement gyro turn control
 ** Actually use encoders
 ** Use a command queue?
 ** Implement D loop
 */

#define TELEMETRY 1
const uint32_t led = 13;
  // This is the pin that the LED on the board goes on
const uint32_t bMillisDelay = 100;
  // This is the delay that starting would have in order not to damage the motors.
const uint32_t stopDelay = 40;
  // This is the delay that the micromouse takes when it's stopping to make sure that the motors are working correctly
const uint32_t uDelay = 625;
  // This is the delay for taking u-turns.
const uint32_t lDelay = 325;
const uint32_t rDelay = 350;
const uint32_t stopRead = 450;// how it tells whether the wall is right in front of it or not
const uint32_t forwardSpeed = 200; // default forward speed
const uint32_t turnSpeed = 30; // default turning speed
const uint32_t turnRead = 750; // how the front sensor says a turn is done
const uint32_t turnThresholdL = 950; // how the side sensors say that something is a turn
const uint32_t turnThresholdR = 950;
const uint32_t activeBrakeTime = 170;
const uint32_t activeBrakeSpeed = 15;
const uint32_t activeTurnBrakeTime = 180;
const uint32_t activeTurnBrakeSpeed = 10;
const uint32_t sensorPinL = A0;
const uint32_t sensorPinR = A2;

unsigned long lLastMillis;  // We use this variable later on for timed backing up...
#define FORWARD 0 // Define forward so that the operator doesn't get confused about which direction the mouse is headed in.
#define BACKWARD 1 // Same with backward
#include "mctrl.h" // include the class description of the mouse
#include "encodr.h"
#include "fill.h"
enum eStates { eForward = 1, eTurnU = 2, eTurnL = 3, eTurnR = 4 }; // Enumerate the states that the upper finite-state machine can be in
void w8 (const uint32_t w8Time) {
  lLastMillis = millis();
  do {  } while ((millis() - lLastMillis) <= w8Time );
}
void setup() {
  for (uint32_t i = 5; i <= 10; i++) { // use a for loop to init. the pins of the microcontroller
    pinMode (i, OUTPUT); 
  }
  pinMode (led, OUTPUT); // init the LED pin correctly
  pinMode (A0, INPUT);  // have the sensors 
  pinMode (A1, INPUT);
  pinMode (A2, INPUT);
  pinMode (A5, INPUT);
  pinMode (A6, INPUT);
  pinMode (0, OUTPUT);
  pinMode (1, INPUT);
  pinMode (11, INPUT);
  pinMode (12, INPUT);
  attachInterrupt(11, lMotorInc, CHANGE);
  attachInterrupt(12, rMotorInc, CHANGE);
  delay(1000);
  delay(1000);
  delay(1000); // put a delay here so that the mouse won't go springing off immediately after turning on
#if TELEMETRY
  Serial1.begin(9600);
#endif
}
mCtrl faulhaber(forwardSpeed, FORWARD, 7, 8, 9, 10, bMillisDelay, 10.00, 15);
// this syntax is a little confusing.  so I'll break it down.
/*    default motor speed,
      default motor direction,
      L motor control
      R motor control
      L motor PWM
      R motor PWM
      millisecond delay for soft starts and pid
      P value
      I value
      D value
      initial sensor sample size
*/

// These are calculated encoder counts for wall determination. 220 should be the time that it takes to stop the mouse using delays.
encodr enc(270,200,50);

const char _navRandomness[] = {0x9a, 0x81, 0x47, 0x6b, 0x81, 0xbe, 0xb0, 0xf0,
                               0xdc, 0x18, 0x4f, 0x44, 0x9f, 0x62, 0xe8, 0x5a,
                               0xda, 0x6a, 0x7e, 0x08, 0x18, 0x22, 0x6f, 0x95,
                               0x2e, 0xbc, 0xa3, 0x91, 0x15, 0xa1, 0x9c, 0xfd};

boolean Nav_GetRandomBit() {
	static char seed = 0;
	unsigned char this_ = seed & (8-1);
	unsigned char that = _navRandomness[seed/8];
	++seed;
	this_ >>= that;
	this_ &= 0x01;
	
	
	
	return this_;
}

void loop() {
  static boolean delayed = 0;
  unsigned long time = millis();
  static eStates eState_t; // use enumerated states
  static int inputL = 0;
  static int inputR = 0;
  static boolean enableHoldBack =  0;
  static boolean t = 0;
  while (t == 0) {
 #if TELEMETRY
    Serial1.println("Calibrate!");
 #endif
    faulhaber.calibrateSensors();
    t++;
  }
  boolean stahpLoop = 0;
  uint32_t sensorL = 0;
  uint32_t sensorR = 0;
  switch (eState_t) {
    case eForward:
      digitalWrite(led, HIGH); // we have the LED on for a nice display
      faulhaber.frictionStop(); // we have it stop by the friction generated by the motors
      faulhaber.switchDirection(FORWARD); // in case things before were set to backward or left or something of that sort, we can set things here to whichever side we want (forward).
      faulhaber.changeSpeed(forwardSpeed);
      faulhaber.speedUp(); // soft speedup to get things rolling
      do {
        time = millis();
        delayed = 0;
        sensorL = analogRead(sensorPinL);
        sensorR = analogRead(sensorPinR);
        faulhaber.straightLine(sensorL, sensorR); // use the control algorithm to have things work as they should
        if (enc.cellMark()) {
          Serial1.println("WALL!");
        }
        if (enc.turnOk()) {
          Serial1.println("Turn considered.");
          boolean turnNow = turnNow++;
          if (sensorL > turnThresholdL && turnNow ) {
            stahpLoop = 1;
            enc.forceMark();
            eState_t = eTurnL;
            Serial1.println("TURNING LEFT");
          } else if (sensorR > turnThresholdR && !turnNow ) {
            stahpLoop = 1;
            eState_t = eTurnR;
            enc.forceMark();
            Serial1.println("TURNING RIGHT");
          }
        }
        while (millis() - time < 10) {
          delayed = 1;
        }
        if (!delayed) {
          Serial1.println("Not delayed!");
        }
      } while ((analogRead(A1) > stopRead) && (!stahpLoop)); // When we get close enough to the wall, stop.
      faulhaber.changeSpeed(activeBrakeSpeed);
      faulhaber.layInSpeed();
      faulhaber.switchDirection(BACKWARD);
      w8(activeBrakeTime);
      faulhaber.frictionStop();
      w8(stopDelay);
      if (stahpLoop) {
        stahpLoop = 0;
        Serial1.println("Check.");
        break;
      }   
      sensorL = analogRead(A0);
      sensorR = analogRead(A2);
#if TELEMETRY
      Serial1.print("Left ENC: ");
      Serial1.println(enc.lMotorEnc);
      Serial1.print("Right Enc: ");
      Serial1.println(enc.rMotorEnc);      
      Serial1.print("Left Sensor: ");
      Serial1.println(sensorL);
      Serial1.print("Right Sensor: ");
      Serial1.println(sensorR);
#endif
      if (sensorL > turnThresholdL && sensorR > turnThresholdR) {
#if TELEMETRY
        Serial1.println("R turn!");
#endif
        eState_t = eTurnR; // After this, we want to be turning 180 degrees
      } else if (sensorR > turnThresholdR) {
#if TELEMETRY
        Serial1.println("Turning Right.");
#endif
        eState_t = eTurnR;
      } else if (sensorL > turnThresholdL) {
#if TELEMETRY
        Serial1.println("Turning Left.");
#endif
        eState_t = eTurnL;
      } else {
        eState_t = eTurnU;
#if TELEMETRY
         Serial1.println("U turn!");
#endif
      }
    break;
    case eTurnU:
      digitalWrite(led, LOW); // Turn the LED off so that we know that it's trying to go backwards
      faulhaber.frictionStop();
      faulhaber.turnAround(0); // make the motor control pins go backward
      faulhaber.changeSpeed(turnSpeed);
      faulhaber.layInSpeed();
      w8(uDelay);
      faulhaber.turnAround(1);
      faulhaber.changeSpeed(activeTurnBrakeSpeed);
      faulhaber.layInSpeed();
      w8(activeTurnBrakeTime);
      eState_t = eForward; // loop to go forward again
      enc.forceMark();
    break;
    case eTurnL:
      digitalWrite(led, LOW);
      faulhaber.frictionStop();
      faulhaber.turnAround(0);
      faulhaber.changeSpeed(turnSpeed);
      faulhaber.layInSpeed();
      w8(lDelay);
      faulhaber.turnAround(1);
      faulhaber.changeSpeed(activeTurnBrakeSpeed);
      faulhaber.layInSpeed();
      w8(activeTurnBrakeTime);
      eState_t = eForward;
      enc.forceMark();
    break;
    case eTurnR:
      digitalWrite(led, LOW);
      faulhaber.frictionStop();
      faulhaber.turnAround(1);
      faulhaber.changeSpeed(turnSpeed);
      faulhaber.layInSpeed();
      w8(rDelay);
      faulhaber.turnAround(0);
      faulhaber.changeSpeed(activeTurnBrakeSpeed);
      faulhaber.layInSpeed();
      w8(activeTurnBrakeTime);
      eState_t = eForward;
      enc.forceMark();
    break;
    default:
      eState_t = eForward;
    break;
  }
}

void lMotorInc() {
  enc.lMotorInc();
}

void rMotorInc() {
  enc.rMotorInc();
}

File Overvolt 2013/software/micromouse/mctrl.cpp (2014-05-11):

#include "Arduino.h"
#include "mctrl.h"
#define DEBUGMODE 0

/* This is the constructor function.
 * 
 * The constructor should take arguments and make them work properly.
 * The .h file has better data on what everything here actually does and things of that sort.
 **/
mCtrl::mCtrl(const byte iMotorSpeed, const boolean oDirection,
 const byte bMotorLeftPin, const byte bMotorRightPin,
 const byte bMotorLeftPWM, const byte bMotorRightPWM, 
 const unsigned long bMillisDelay, const float fP, 
 const byte bSampleSize)
{
  /* for a detailed documentation on what each one of these values
  is, I suggest you read the .h file. */
  this->bMotorLeftPin = bMotorLeftPin;
  this->bMotorRightPin = bMotorRightPin;
  this->bMotorLeftPWM = bMotorLeftPWM;
  this->bMotorRightPWM = bMotorRightPWM;
  this->bMotorLeftSpeedGoal = iMotorSpeed;
  this->bMotorRightSpeedGoal = iMotorSpeed;
  this->switchDirection(oDirection); // call the switchDirection function to put the motors in the correct direction
  this->bMillisDelay = bMillisDelay;
  this->fP = fP;
  this->bSampleSize = bSampleSize;
  this->calibrateSensors();  // Calibrate the sensors.  That's what we'll have to initially do
  this->lSensorPIDIgnore = 800;
  this->rSensorPIDIgnore = 800;
}


/*
 * This is the switch direction function.
 *
 * I have gone through and there really is no reason to have signed motor control unless I were completely insane.
 * I'm not saying that I'm not completely insane, just to clarify.
 **/
void mCtrl::switchDirection(const boolean oDirection) {
  this->oDirection = oDirection;
  if (this->oDirection == 1) { // Clearly, the "right" direction is backwards.
    digitalWrite(this->bMotorLeftPin, LOW); // these are the pin settings to get everything to go backward
    digitalWrite(this->bMotorRightPin, LOW);
  } else {
    digitalWrite(this->bMotorLeftPin, HIGH); // these are the pin settings to make everything go forward
    digitalWrite(this->bMotorRightPin, HIGH);
  }
}


/*
 * This is the motor speed return statement.  This basically takes two of the motorSpeedGoals
 * and divides them by two to get the motor speed for everything. 
 **/
const byte mCtrl::motorSpeedGoal() const{
  unsigned int iReturn = ((this->bMotorLeftSpeedGoal + this->bMotorRightSpeedGoal) / 2);

  // Return the average speed.
  return iReturn;
}


/*
 * This is the actual motor speed.  Ideally, we should have the microcontroller set it at the goal all the time, but this is not possible because of system error.
 **/
const byte mCtrl::motorSpeedAt() const{
  unsigned int iReturn = ((this->bMotorLeftCurrent + this->bMotorRightCurrent) / 2);
  return iReturn; // return the average value of the motors' current set speed
}

void mCtrl::speedUp() {
  unsigned long lLastMillis = millis();; // use the elapsedMillis datatype to simplify coding for these sorts of things
  for (byte i = this->motorSpeedAt(); i <= this->motorSpeedGoal(); i++) {

    // for each value until the set value, speed up the motors uniformly
    this->bMotorLeftCurrent = i;
    this->bMotorRightCurrent = i;

    // Write the values to the motors.
    analogWrite(this->bMotorLeftPWM, this->bMotorLeftCurrent);
    analogWrite(this->bMotorRightPWM,this->bMotorRightCurrent);

    // This is just the delay that we use before the task scheduler is implemented... which it will be some day...
    do {} while (lLastMillis - millis() <= bMillisDelay);
    lLastMillis = millis();
  }
}

void mCtrl::slowDown() {
  // Set a variable to store our run time
  unsigned long lLastMillis = millis();

  // Slow things down until they are zero.
  for (byte i = this->motorSpeedAt(); i != 255; i--) {

    // Set the speed of the motors.
    this->bMotorLeftCurrent = i;
    this->bMotorRightCurrent = i;

    // Write the speed of the motors.
    analogWrite(this->bMotorLeftPWM, bMotorLeftCurrent);
    analogWrite(this->bMotorRightPWM, bMotorRightCurrent);

    // We use our processor consuming loop once again... SAY, WHERE THE HECK IS THAT SCHEDULER?
    do { } while (lLastMillis - millis() <= bMillisDelay);
    lLastMillis = millis();
  }
}

/*
 * Here we have the almighty P algorithm.
 * (I and D should be coming back from the depths of oblivion eventually...)
 *
 **/
void mCtrl::straightLine(const uint32_t & lSensorRead, const uint32_t & rSensorRead) { // here's the interesting stuff with proportional control.

  /*
   * Here we have variable.
   *
   * First, we have the delay variable.
   * Second, we have the mouse error variable.
   *
   **/
  unsigned long ePassedMillis = millis();
  static int iMouseError = 0;

 /*
  * Let me talk about what debug mode and what it does...
  * Debug mode prints out the PID function in...
  * R: <right sensor value>L: <left sensor value> <Sensor usage message>E: <mouse error>
  **/

#if DEBUGMODE
  Serial1.print("R ");
  Serial1.print(rSensorRead);
  Serial1.print("L ");
  Serial1.print(lSensorRead);
#endif

  // Here come the conditions in which the sensors can reach
  // In this condition, we ignore everything because the sensors are out of range.
  bool lSensorInRange = lSensorRead <= lSensorPIDIgnore;
  bool rSensorInRange = rSensorRead <= rSensorPIDIgnore;
  if (!lSensorInRange && !rSensorInRange) {
    iMouseError = 0;
#if DEBUGMODE
    Serial1.print(" N");
#endif
  // In this condition, we assume that the left wall is missing.
  } else if (!lSensorInRange && rSensorInRange) {
    iMouseError = -2*(rSensorRead - this->rightSensorCalibrate );
#if DEBUGMODE
    Serial1.print(" R");
#endif
  // In this condition, we assume that the right wall is missing.
  } else if (!rSensorInRange && lSensorInRange) {
    iMouseError = 2*(lSensorRead - this->leftSensorCalibrate );
#if DEBUGMODE
    Serial1.print(" L");
#endif
  // If all is good, we use both sensors... LIKE A BOSS.
  } else {
    iMouseError = ((lSensorRead - this->leftSensorCalibrate) - (rSensorRead - this->rightSensorCalibrate)); 
    iMouseError /= (2);
#if DEBUGMODE
    Serial1.print(" A");
#endif
  }

  // Let's calculate and initiatie the correction factor.
  int32_t correctionFactor = (this->fP * iMouseError);
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

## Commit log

2013-06-06 I added my crappy code. Feel free to make it not work any more. The functions are not yet set in stone.
    [encodr.cpp, mctrl.cpp, micromouse.ino]
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2013-07-20 Added power supply schematic and link to more mouse code
    [TPS62056_Reference.kicad_pcb, TPS62056_Reference.sch]
2013-07-23 Found parts, created footprints, added to board.
    Board had all footprints on it, but it completely rat's nest.
    Spreadsheet BOM created, but not yet in repo.
    [TPS62056_Reference.kicad_pcb, TPS62056_Reference.sch]
2013-07-24 Board is almost completely routed
    Except for an error that prevents me from connecting anything to the
    IC...
    [TPS62056_Reference.kicad_pcb, TPS62056_Reference.sch]
2013-07-24 Board completed
    Added silkscreen help and connected the rest of the pins
    [TPS62056_Reference.kicad_pcb]
2013-07-24 Added BOM
    [Project BOMs.xlsx]
2013-07-24 Fixed some minor errors in BOM
    [Project BOMs.xlsx]
2013-07-24 Added more via stitching and gerbers
    More via stitching between front & back ground plane and adjusted planes
    to fit vias.
    [TPS62056_Reference-B_Cu.gbl, TPS62056_Reference-B_Mask.gbs, TPS62056_Reference-B_SilkS.gbo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]
2013-07-24 Moved silkscreen to so that it's not broken by vias. Added PDF of schem and board.
    [TPS62056_Reference-B_Cu.gbl, TPS62056_Reference-B_Mask.gbs, TPS62056_Reference-B_SilkS.gbo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]
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2013-08-08 I finally did something: add documentation and begin creating some of the interfaces to the STM32 chip.
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2013-08-26 RefMouse1 stuff
    Added datasheets and started schematic
    [$RefMouseV1.sch, RefMouseV1-Power.sch, RefMouseV1.kicad_pcb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]
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2013-09-04 More reference mouse pcb stuff
    [$RefMouseV1.sch, RefMouseV1-Power.sch, RefMouseV1.sch]
2013-09-17 Added gearbox.
    [Mechanics Assembly.0012.iam, Mechanics Assembly.iam, Spur Gear12.ipt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]
2013-09-19 mount rev2: changed dimensions around and mountin
    [mount.0005.ipt, mount.0006.ipt, mount.ipt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]
2013-09-21 Moved 3D modeling into reference mouse v1 folder.
    Added McMasterCarr parts.
    [7804K129.0001.IPT, 7804K129.IPT, 7804K129.SLDPRT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]
2013-10-05 More 3D modeling done!
    [7804K129.0001.IPT, 7804K129.0002.IPT, 7804K129.IPT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]
2013-10-08 Added DRV sch symbol and motor sub-schematic.
    [RefMouseV1-Motor.sch, RefMouseV1-Power.sch, RefMouseV1.kicad_pcb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]
2013-11-15 Added Sensors in AutoCad
    [Kingbright_WP7113F3BT_Emitter.0002.ipt, Kingbright_WP7113F3BT_Emitter.ipt, LTR_4206E_Photodiode.ipt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]
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2014-04-18 Added datasheets
    [EP4CE15.xls]
2014-04-18 Added datasheets and folders for reference mouse v2
    [Main Assembly.0003.iam, Main Assembly.iam, Pololu Metal Gearmotor.0003.ipt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]
2014-04-18 Rearranged folder structure so that projects are top-level
    [7804K129.0002.IPT, 7804K129.IPT, 7804K129.SLDPRT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]
2014-04-18 Removed old directory structure
    [7804K129.0002.IPT, 7804K129.IPT, 7804K129.SLDPRT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]
2014-04-21 Began development on FPGA mouse board internals.
    This seems difficult.
    [Nyan Mouse.sch, TPS62056_Production.sch, fpga_not_sane.sch]
2014-04-21 Added all FPGA parts and updated excel sheet of pinout.
    [EP4CE15.xls, fpga_not_sane.sch]
2014-04-21 Commiting with corrected file paths
    [Nyan Mouse.sch, TPS62056_Production.sch, fpga_not_sane.sch]
2014-04-22 Schematic things have been updated
    [Nyan Mouse.sch, TPS62056_Production.sch, fpga_bank_ab.sch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]
2014-04-23 A lot of kicad.... A LOT.
    [BIGBOOM_SENSORS.sch, Nyan Mouse.sch, TPS62056_Production.sch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]
2014-04-23 Did a 3D drivetrain on refmouse 2
    [Main Assembly.0003.iam, Main Assembly.iam]
2014-04-24 Made changes to board 20% done still. :/
    [BIGBOOM_SENSORS.sch, Nyan Mouse.sch, TPS62056_Production.sch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]
2014-04-24 Changed DRV8837, Almost completed main board. ERC almost successful.
    [BIGBOOM_SENSORS.sch, Nyan Mouse.sch, TPS62056_Production.sch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]
2014-04-24 Changed directory structure, where did the fpga board go?
    [BIGBOOM_SENSORS.sch, Nyan Mouse.sch, TPS62056_Production.sch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]
2014-04-24 re-added the fpga parts... I wonder where everything went o.0
    [Nyan Mouse Daughter.sch]
2014-04-24 Finalized connector structure.
    [BIGBOOM_SENSORS.sch, Nyan Mouse Daughter.sch, Nyan Mouse.sch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]
2014-04-24 Okay, now the connector is finalized.
    [Nyan Mouse.sch]
2014-04-24 Git says some inventor files changed, so here
    [AS5000-MR.ipt, Main Assembly.0005.iam, PCB.ipt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]
2014-04-24 Flipped some RGB leds, added emitter pulldowns
    [BIGBOOM_SENSORS.sch, Nyan Mouse.sch, TPS62056_Production.sch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]
2014-04-24 Repopulated FPGA portions...
    Where did my changes go?
    [Nyan Mouse Daughter.sch, fpga_bank_1_2.sch, fpga_bank_3_4.sch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]
2014-04-24 Added bank names to FPGA
    [BIGBOOM_SENSORS.sch, Nyan Mouse.sch, TPS62056_Production.sch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]
2014-04-26 Added ESD prevention documentation.
    Added ByteBlaster documentation.
    Modified FPGA banks.
    [BIGBOOM_SENSORS.sch, Nyan Mouse Daughter.sch, Nyan Mouse.sch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]
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2014-04-26 Added DAC and amp.
    Changed connector spec. for DAC and amp. Sorry guys.
    [BIGBOOM_SENSORS.sch, Nyan Mouse.sch, TPS62056_Production.sch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]
2014-04-26 Did a bit of schematic labeling.
    [Nyan Mouse Daughter.sch, Nyan Mouse.sch, fpga_bank_1_2.sch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]
2014-04-26 Removed backup files and added backup files to git exclude.
    Also added FPGA processor (not done yet).
    [nyan_mouse.csv]
2014-04-27 Created I2C component (will be changed later because of errors).
    Add I2C to board connector on main board (daughter board yet to be done).
    [Nyan Mouse.sch, nyan_mouse.csv]
2014-04-28 Updated schematic and added craptons of symbols.
    [BIGBOOM_SENSORS.sch, Nyan Mouse.sch, TPS62056_Production.sch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]
2014-04-29 Updated schematics
    [$Nyan Mouse.sch, BIGBOOM_SENSORS.sch, Nyan Mouse Daughter.sch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]
2014-04-30 Reverted Refmouse2 Spacer to original size
    [Main Assembly.0005.iam, Main Assembly.iam, Spacer.0001.ipt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]
2014-05-03 Made changes that I forgot about... sorry guys
    [BIGBOOM_SENSORS.sch, Nyan Mouse.sch, TPS62056_Production.sch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]
2014-05-10 Made wheel bigger on RefMouse2
    [Main Assembly.0006.iam, Spacer.0002.ipt, Spacer.stl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]
2014-05-10 MAde D-shaft on wheel larger
    [Wheel Printable.0001.ipt, Wheel Printable.ipt, Wheel Printable.stl]
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2014-05-11 Committing the few things that have been changed these weeks
    [TPS62056_Production.sch]
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
